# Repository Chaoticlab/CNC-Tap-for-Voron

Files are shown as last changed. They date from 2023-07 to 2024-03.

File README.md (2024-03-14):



## *Designed for VORON2.4 R2 and VORON Trident, In honor of the VORON Design*  
## CNC Tap for Voron
**Note:** CNC Voron Tap circuit module is 5V ONLY.  
**CNC Voron Tap Rail**: [Replacement Guide](https://www.youtube.com/watch?v=EFNEYZ-nvDA&t=15s)  
**Sensor Specifications**: [Specifications](Images/Specifications)  
**CNC VORON TAP Build Manual**: [Manual](Manual/CNC_Voron_Tap_Build_Guide.pdf)  
## CNC Tap for Voron V2
**CNC VORON TAP V2 Build Manual**: [Manual](Manual/CNC_VORON_TAP_V2_BUILD_GUIDE_20240222.pdf)  
**CNC VORON TAP V2 中文说明书**: [说明书](Manual/CNC_VORON_TAP_V2_用户手册_20240222.pdf)

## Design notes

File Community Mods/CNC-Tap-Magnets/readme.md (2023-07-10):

Voron Tap r8 style magnet mounts for Chaoticlab's CNC TAP

Initial release by Telani#9207

Tip jar at https://www.patreon.com/TidyPrints

This is a remix of the most recent Tap R8 release with the 2.4r2 hot end rear mount parts. The goal is to get additional stability on the CNC TAP by adding Voron Tap r8 styled/angled magnets to the assembly. I didn't end up doing as much benchmarking of this vs tap r8 as I had intended, but I'm getting 5500 y axis automatic tunes when before magnets I had issues breaking 3200 on y axis, both using the fixed higher preload rail. I'm releasing this early without much testing in the hopes that others will have ideas for ways to do this better.

BOM:

2x M3x6 BHCS (button head) to replace the M3x5 SHCS (cap head) at the belt mounts

2x M3 washers

2x M3x10 BHCS

2x M3x5x4 Heat Set Inserts (Voron Inserts)

2x (or 4x) 6mm x 3mm neodymium magnets, I am using 4x N52

2x (or 0x) M3x6 FHCS

STLs:

1x of left belt mount

1x of right belt mount

1x of left magnet pod

1x of right magnet pod

1x of your hot end's rear mount from the hot ends folder

Check the voron tap manual here for magnet pod assembly and general tips on alignment: https://github.com/VoronDesign/Voron-Tap/blob/main/Manual/Assembly_Manual_Tap.pdf

Belt mounts are best installed with a/b drive belt tension at minimum, with the slack on the left of the print head. AKA, install the right belt mount first. I find it easier to attach the CNC TAP to the rail only after attaching the belt mounts.

Overtightening any of the fastners that secure plastic to metal can cause part warping, be careful not to over tighten things. 

Install magnet pods at the farthest back spot before installing the hot end, after assembly release then tighten the magnets while gently pulling the hot end downwards. Make sure the switch audibly clicks when the hot end returns to it's default position. Improperly installed magnets can be worse than none.

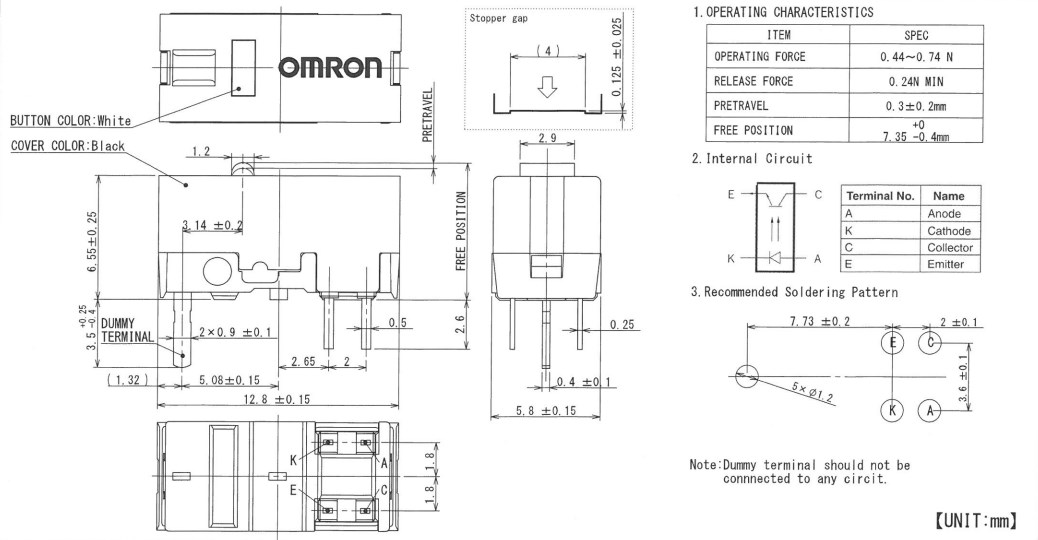
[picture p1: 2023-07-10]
Images/Specifications/Product Specification_D2FP-FN(1)_1.jpg

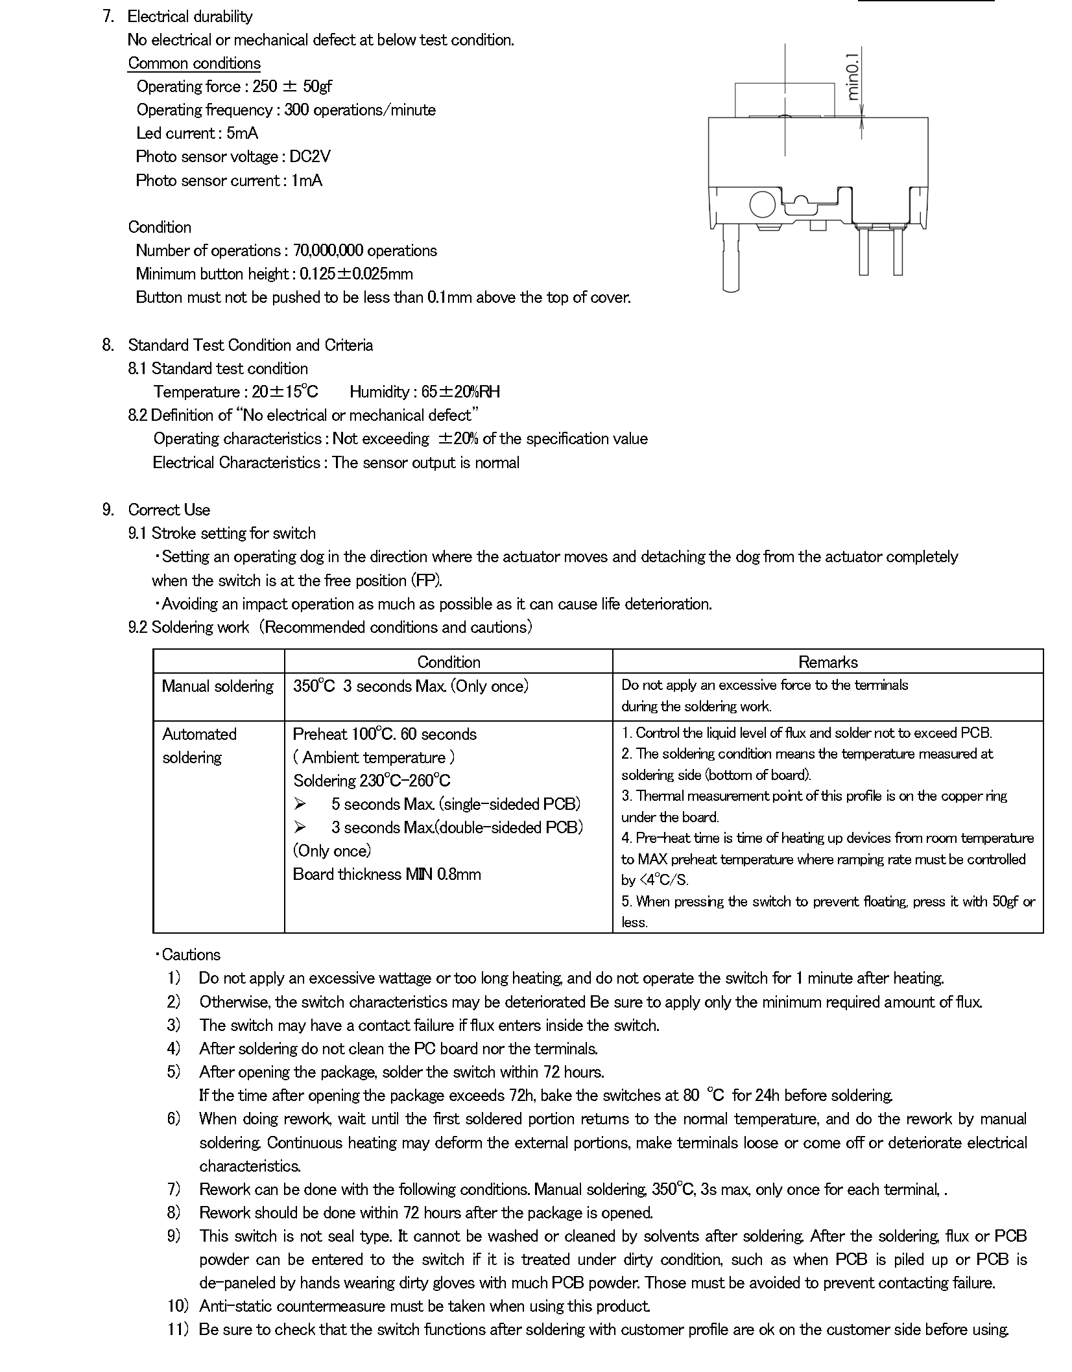
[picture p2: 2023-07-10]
Images/Specifications/Product Specification_D2FP-FN2(1)_5.png

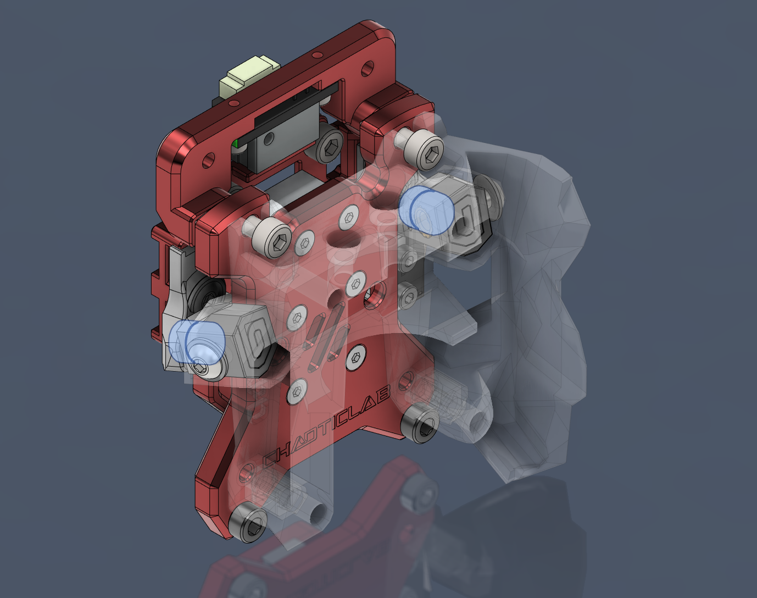
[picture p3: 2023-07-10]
Community Mods/CNC-Tap-Magnets/cnctapmagnets.png

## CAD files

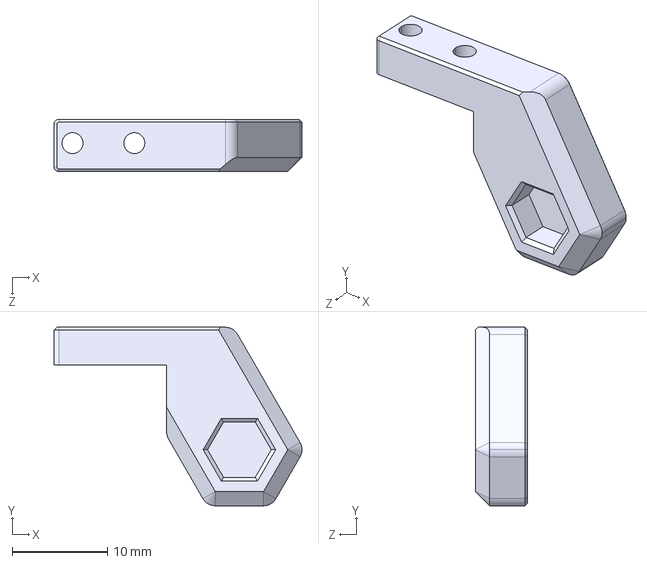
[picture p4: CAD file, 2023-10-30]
CAD/CNC_VORON_TAP_V2/V2 Hall Sensor Adapter.STEP
26.1 x 18.8 x 5.50 mm

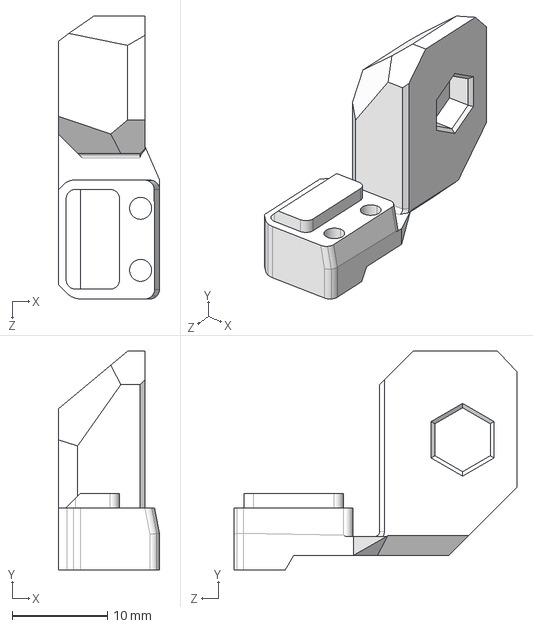
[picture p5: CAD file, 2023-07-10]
CAD/XY_Switch_Adapter/CNC_Voron_TAP_XY_Switch_Adapter_V2.step
10.6 x 22.9 x 29.6 mm

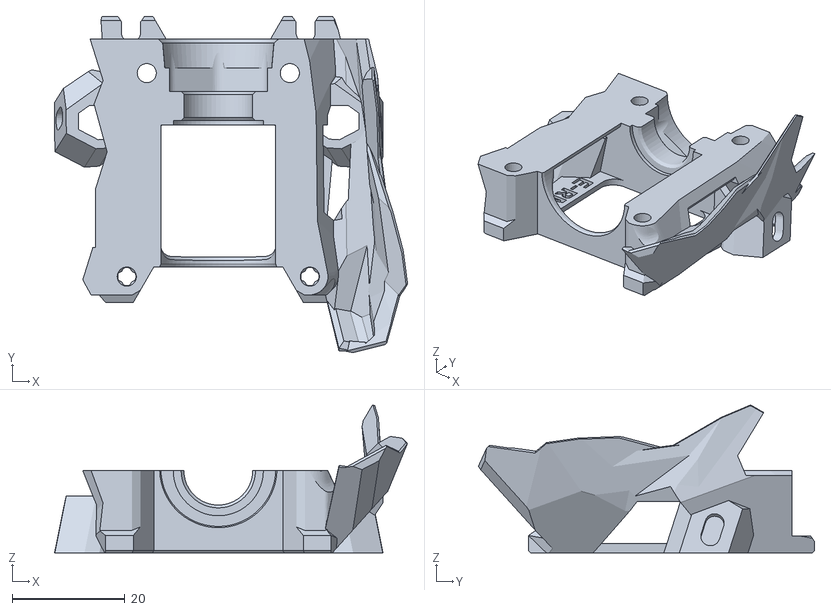
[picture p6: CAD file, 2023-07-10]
Community Mods/CNC-Tap-Magnets/hot ends/revo micro.stl
62.7 x 59.7 x 26.3

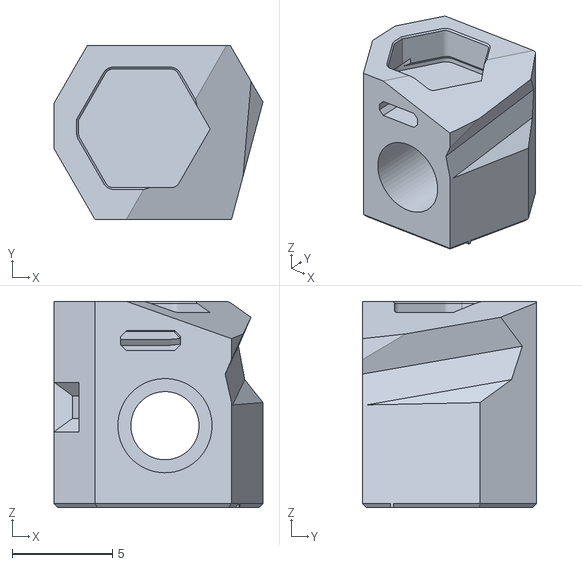
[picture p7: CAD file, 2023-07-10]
Community Mods/CNC-Tap-Magnets/right magnet pod.stl
10.4 x 8.70 x 10.3

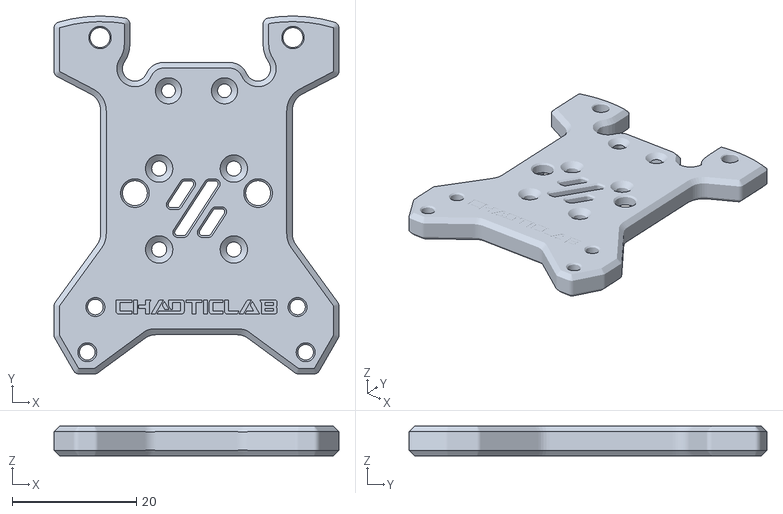
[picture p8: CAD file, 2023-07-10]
STL/CNC_VORON_TAP/Tool head mounting plate.STL
45.8 x 57.5 x 4.78

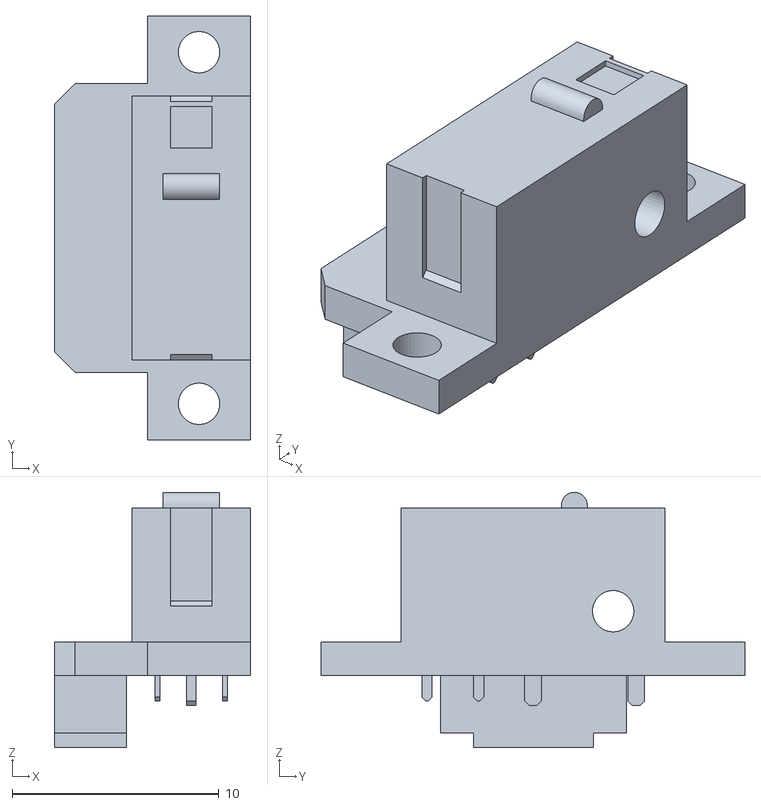
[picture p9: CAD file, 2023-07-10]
STL/Sensor/CNC_Tap_Sensor.STL
9.50 x 20.5 x 12.4

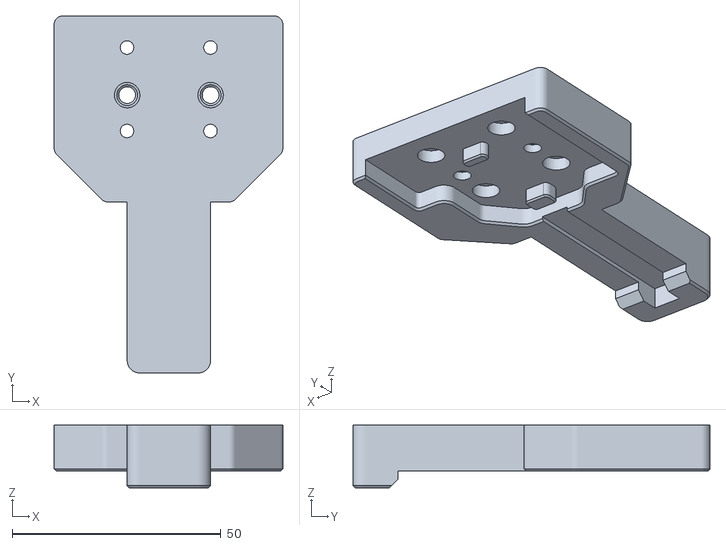
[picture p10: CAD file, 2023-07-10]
STL/XY_Switch_Adapter/Slider Block Installation Tool.STL
54.8 x 85.6 x 15.0

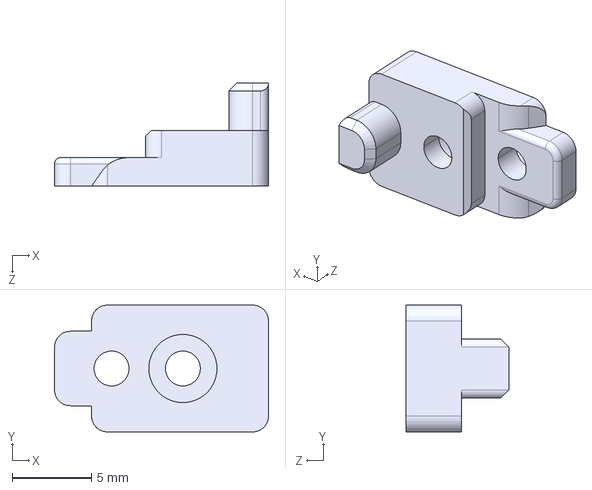
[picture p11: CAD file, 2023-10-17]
CAD/CNC_VORON_TAP_V2/V2 Bracket Adapter.STEP
13.5 x 8.00 x 6.50 mm

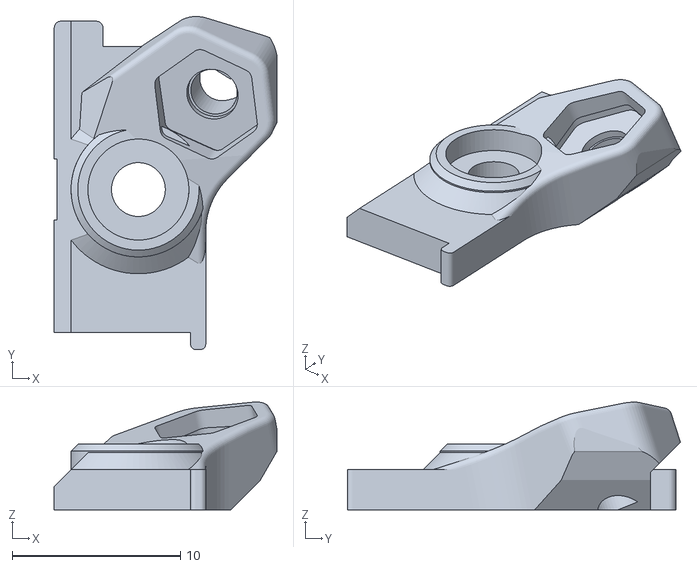
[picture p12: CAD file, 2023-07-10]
Community Mods/CNC-Tap-Magnets/left belt mount.stl
13.2 x 19.8 x 6.40

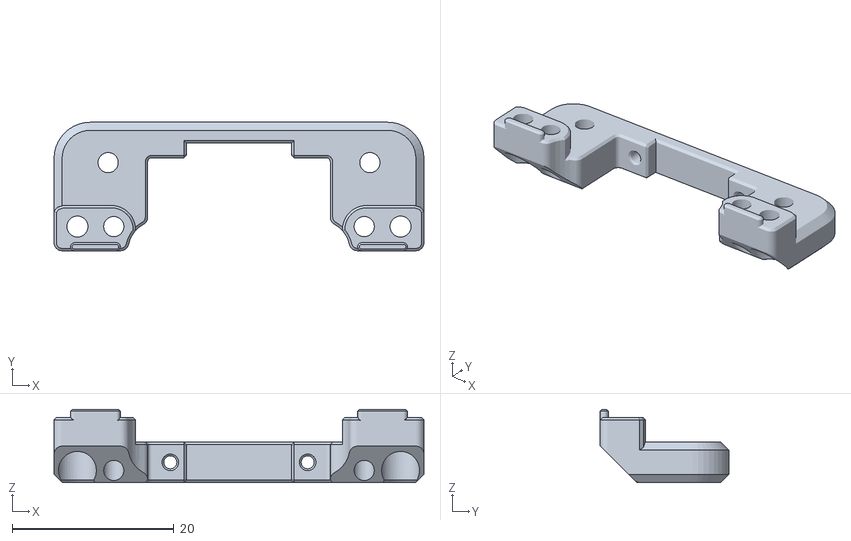
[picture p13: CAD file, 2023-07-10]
STL/CNC_VORON_TAP/Sensor fixing seat.STL
45.8 x 15.9 x 9.05

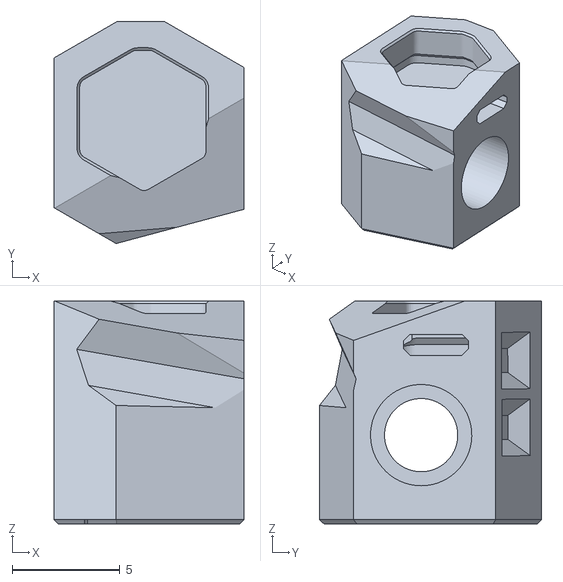
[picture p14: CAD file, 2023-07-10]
Community Mods/CNC-Tap-Magnets/left magnet pod.stl
8.80 x 10.3 x 10.3

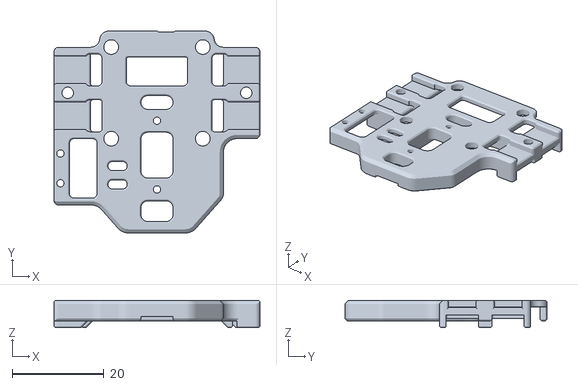
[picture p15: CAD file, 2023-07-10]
STL/CNC_VORON_TAP/x carriage center.STL
45.0 x 44.1 x 6.00

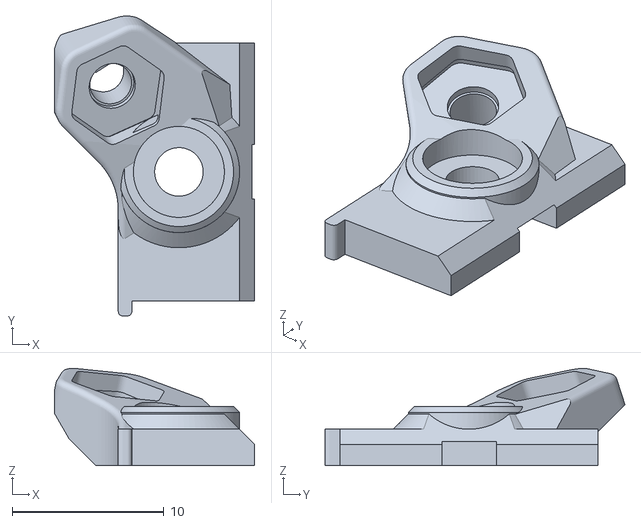
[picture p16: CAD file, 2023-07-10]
Community Mods/CNC-Tap-Magnets/right belt mount.stl
13.2 x 19.8 x 6.40

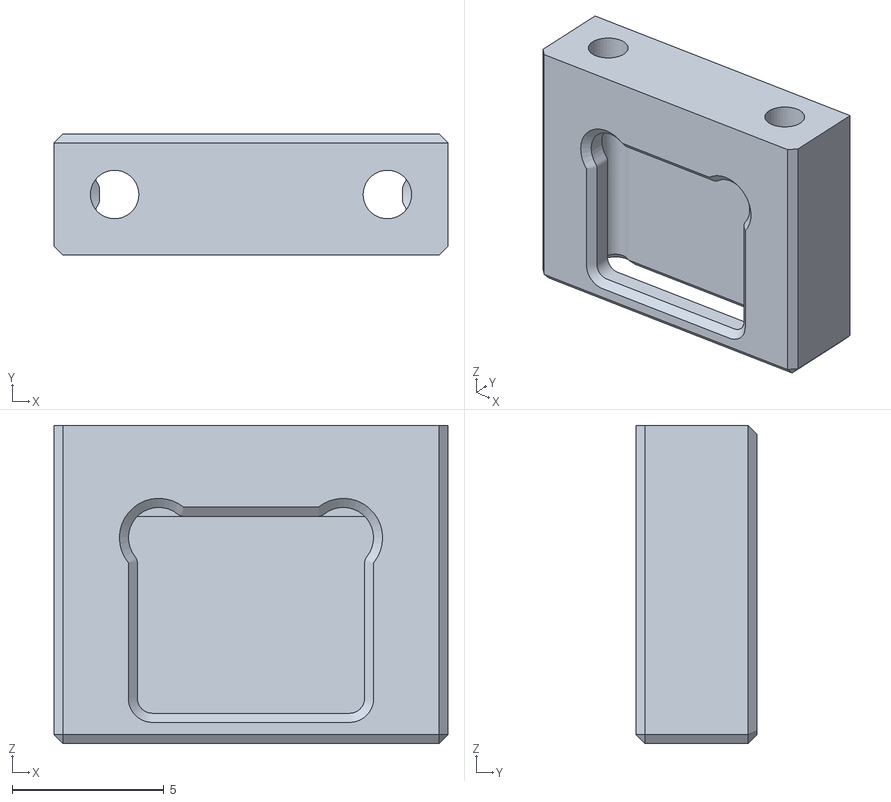
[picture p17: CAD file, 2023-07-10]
STL/CNC_VORON_TAP/Magnet bracket.STL
13.0 x 4.00 x 10.5

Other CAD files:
Community Mods/CNC-Tap-Magnets/hot ends/dragon.stl
Community Mods/CNC-Tap-Magnets/hot ends/phaetus bms 6fin.stl
Community Mods/CNC-Tap-Magnets/hot ends/phaetus bms 7fin.stl
Community Mods/CNC-Tap-Magnets/hot ends/phaetus bmo.stl
Community Mods/CNC-Tap-Magnets/hot ends/rapido.stl
Community Mods/CNC-Tap-Magnets/hot ends/revo voron.stl
STL/CNC_VORON_TAP/Belt pressure plate.STL
STL/CNC_VORON_TAP_V2/V2 Bracket Adapter.STL
STL/CNC_VORON_TAP_V2/V2 Hall Sensor Adapter.STL
STL/XY_Switch_Adapter/CNC_Voron_TAP_XY_Switch_Adapter_V2.stl

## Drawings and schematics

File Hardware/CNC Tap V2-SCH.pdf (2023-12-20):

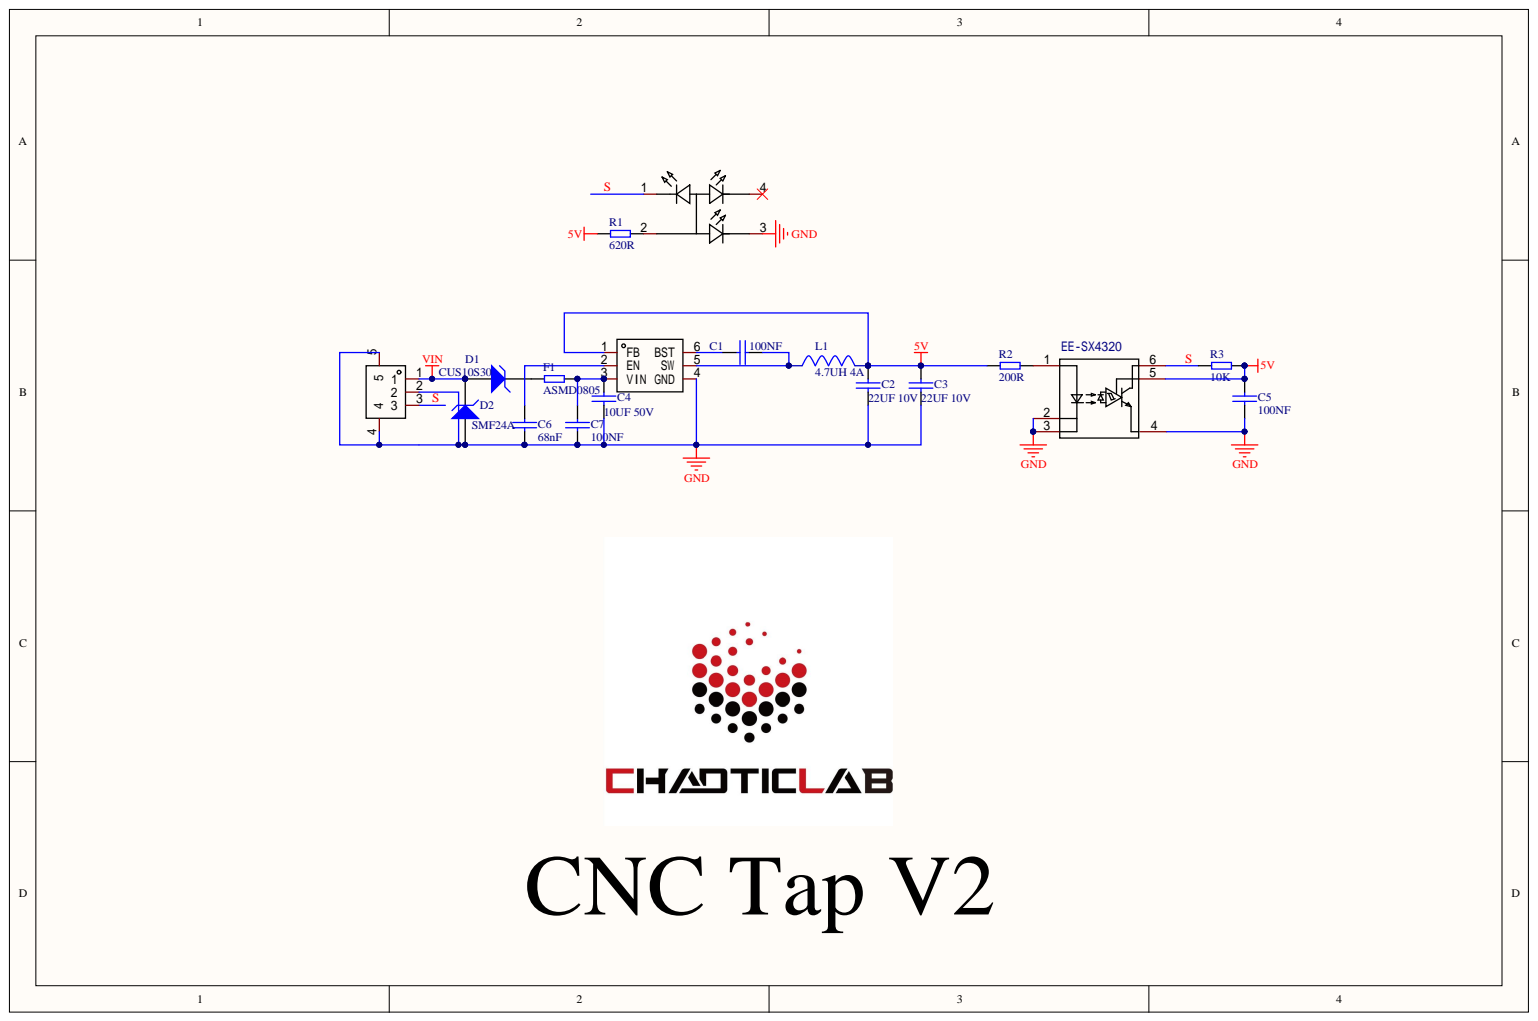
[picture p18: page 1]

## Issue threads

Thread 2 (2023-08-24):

Cnc tap R8 feedback

PuszInPusz, 2023-08-24:
Hey Chaoticlab team, I just wanted to ask (maybe even suggest an improvement) on the CNC Tap R8 design mode. Wouldn't it be somewhat better if instead of 4 magnets 2 of them would get replaced by 2 screws? I found some slight problems when probing at higher temperatures with longer soaking times where the probe either triggers prior to movement or just exceeds to tolerances even when they are as high as 0.008mm. By making the magnets not touching each other (while adjusting trough the screw mechanism I put a 0.3mm precision gauge between the magnets) I was able to go as low as 0.001 tolerance and everything seems okay so far. I think the poles of the magnets really work agains each other if the magnets are not like 100% dead on so my hypothesis is by changing 2 of the magnets for steel sunk in screws the problem could be remediated without loosing to much of the performance but maybe making it more reliable.

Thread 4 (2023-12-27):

X-Limit Switch Bracket too Short for Carbon Fiber Gantry Kit

solrac8874, 2023-12-27:
I upgraded my Voron 2.4 with Chaoticlab's Carbon Fiber Gantry kit (A-B motor mounts + XY gantry mounts with 2020 extrusions) and CNC Tap V2.  The Carbon Fiber Gantry kit doesn't support X & Y limit switches on the XY gantry mounts so I relocated the Y-limit switch to the A motor mount per the Carbon Fiber Gantry kit manual.  Works great.

However, when relocating the X-limit switch to the CNC Tap V2 using the included Limit Switch Bracket I found the MGN12 Block hits the upper XY gantry mount plate before the X-limit switch hits the lower XY gantry mount plate/filler block.  Seems the Limit Switch Bracket is short by about 6-8mm to enable the X-limit switch to hit before the MGN12 Block.  Is there a fix for this?
See pictures below.

Front view:
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

My thumbnail is where the MGN12 Block hits the upper XY gantry mount plate.  The straight down the ruler shows the gap preventing the X-limit switch from making contact to the lower XY gantry mount plate/filler block.

Rear view:
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

With my Toolhead moved to max X-position limited by the MGN12 Block hitting the upper XY gantry mount plate, you can see the X-axis limit does not contact the lower XY gantry mount plate/filler block.

The V2 Bracket Adapter and the CNC_Voron_TAP_XY_Switch_Adapter_V2 do not seem to work or I don't see how those could be used for my case.  The adapters seem to be intended for use with the original Voron 2.4 XY-Limit Switch Mount configuration, not for use with Chaoticlab's Carbon Fiber Gantry kit.

I also noticed the original Voron 2.4 XY gantry mounts are flush top & bottom.  Whereas, the Chaoticlab's Carbon Fiber XY Gantry mounts are not; top plate matches the Voron XY gantry mount surface location, but the lower plate does not - source of the problem?

Chaoticlab, 2024-01-05:
Hey bud, thank you for commented this issues, we have design the MOD for help you better installed CNC Voron Tap V2 with carbon fiber kit, please check in this https://github.com/Chaoticlab/CNC-Tap-for-Voron/blob/master/STL/CNC_VORON_TAP_V2/V2%20Bracket%20Adapter.STL

solrac8874, 2024-01-06:
I tried using the CNC_Voron_TAP_XY_Switch_Adapter_V2, but it doesn't seem to work.  Am I installing it wrong?  I assume it screws into the right most (from the pic in my original post) hole of the Tap to extend the X-limit switch bracket to the right.  Unfortunately, I can't get to hole pattern in the Adapter to match up with the Tap right most hole.

Do you have graphic or picture of how the Adapter is installed to the Tap and X-limit switch bracket?

solrac8874, 2024-02-15:
I tried the limit switch bracket in pull request #6 , but it was still a hair short for me.  I modified the bracket design a bit by moving the switch mount holes an additional 2.5mm horizontally and 2mm vertically away from the bracket mount holes.  See attached pictures (orig. vs. mod).  May consider modifying the bracket in pull request #6 accordingly.

Original (from Pull Request #6 )
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

My mod make it work.
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

This issue can be closed once Pull Request#6 is closed.

Thanks for the support.

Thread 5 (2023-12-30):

Stock X endstop doesn't get triggered

YoungHillionaire, 2023-12-30:

EddieGreen, 2024-02-08:
Not sure what you mean by stock endstop, but guessing you mean this:

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

The bolt hole does coincide with the PCB endstop microswitch - something I found out before I CADded the assembly.

I put the design on hold waiting for the V2 CAD model from Chaotic Labs, but in two months, not a word about that.

The V1 bolt positions and the important dimensions are the same between V1 and V2, so I have used the V1 assembly to make progress with the endstop design.

I thought I'd let you know that a design is on it's way - I'll post updates here.

YoungHillionaire, 2024-02-08:
Yes I need something like this to trigger the stock xy endstop

I have microswitches
I didn't want to solder because my soldering is not working

YoungHillionaire, 2024-02-08:
I went to an electronics shop and get mine soldered so problem fixed for me

But they need to add an stl like this picture for people who want to use stock xy endstop

ruxi, 2024-03-22:
+1, also looking for x-endstop solution for ldo's xy pcb

EddieGreen, 2024-03-22:
I created a suitable X-endstop for Chaoticlabs Voron TAP V1-2 (Harkt XY Endstop PCB):

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

BOM: 3no. M3x8 SHCS, 1no. M3 Threaded Insert

[Chaoticlabs Voron TAP V1-2 (Harkt XY Endstop PCB) Trigger.zip](https://github.com/Chaoticlab/CNC-Tap-for-Voron/files/14723534/Chaoticlabs.Voron.TAP.V1-2.Harkt.XY.Endstop.PCB.Trigger.zip)

STEP file attached.

mabl, 2024-03-24:
I just used a long screw that I inserted into the bottom threads of the CNC-Tap. The screw head reliably hits and triggers the LDO XY end stop. I countered the screw with an additional nut.

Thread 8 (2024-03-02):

Hall affect x trigger

Bluediablito, 2024-03-02:
Hello, just installed the tap V2 and printed the hall end top bracket but noticed it does not trigger the sensor. Is there any STL for the voron 2.4 hall affect end stop magnetic sensor?

This is the file I printed
https://github.com/Chaoticlab/CNC-Tap-for-Voron/blob/master/STL/CNC_VORON_TAP_V2/V2%20Hall%20Sensor%20Adapter.STL

Thank you

Bluediablito, 2024-03-03:
Was installing it the wrong way.

Closed 2024-03-03.

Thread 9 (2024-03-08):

Cable wiring for 2209

phpbbireland, 2024-03-08:
If you connect the connector to either of the EBB 2209 boards with orientation shown, V and G will be reversed possibly damaging the sensor board.

phpbbireland, 2024-03-10:
Correct wiring...
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

Mugga6315, 2024-04-12:
I don't think that this is the correct orientation. I did it that way, light from tap is working and in klipper I get reading. But its always triggered when board klipper is started. Even when I switch in config. Seems that maybe G / S have to be switched. But I wanted to check first

hiddengerbil, 2025-02-22:
I have a premade cable, which fits that probe socket, and it has a tap plug and a two pin Filament run-out detector. Is the filament detector still possible with your wiring example?

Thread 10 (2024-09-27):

negative z_offset?

maverickagm, 2024-09-27:
On my original voron tap, I had z_offset set to zero.
With the Chaoticlab CNC Tap V2.0 I had bed adhesion issues until I ran PROBE_CALIBRATE in Klipper and discovered I needed a -0.385mm z_offset.

Intuitively, I would expect the nozzle to hit the bed, the tap sensor to activate, then that would be the zero offset.

Is this normal? How would I account for the negative offset value? Is that the distance the tap travels before triggering? Or does it have to do with latency between the sensor triggering and it being registered with Klipper?

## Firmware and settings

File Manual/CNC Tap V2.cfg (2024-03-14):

[probe]
pin: !PG12 # Actual IO pin you connected to
x_offset: 0
y_offset: 0
z_offset: 0
speed: 5.0
samples: 2
samples_result: median
sample_retract_dist: 3.0
samples_tolerance: 0.05
samples_tolerance_retries: 3

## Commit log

2023-07-10 202230710 for invaild manual
    [Belt pressure plate.STL, CNC VORON TAP BOM v1.0.xlsx, CNC_Tap_Sensor.STL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]
2023-10-17 上传V2中文版说明书
2023-10-30 Upload Mod
    This is a adapter used to be compatible with old hall sensor.
    [V2 Hall Sensor Adapter.STL]
